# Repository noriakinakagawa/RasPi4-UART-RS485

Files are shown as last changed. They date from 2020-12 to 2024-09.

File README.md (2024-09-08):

# RasPi4-UART-RS485
Raspberry Pi 4 のUART 5chをRS485に変換したコマンド式サーボモータを動かすための基板データ

## Raspberry Pi OSの場合
/boot/config.txt or /boot/firmware/config.txt

## Ubuntuの場合
/boot/firmware/usercfg.txt

以下を追加して保存・再起動  
dtoverlay=pi3-miniuart-bt  
dtoverlay=uart0  
dtoverlay=uart2  
dtoverlay=uart3  
dtoverlay=uart4  
dtoverlay=uart5  
//init_uart_clock=169600000 // for RasPi5
  
/dev/ttyAMA0~AMA4の5ポートでRS485通信が可能となります。

## 注意事項
RTS信号をTXDから遅延タイマICを介して生成しているため、汎用的に使う場合は考慮が必要です。

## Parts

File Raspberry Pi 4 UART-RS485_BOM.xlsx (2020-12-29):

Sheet: 部品表
Reference | Quantity | Footprint | Datasheet | 購入URL | 型番 | 数量 | 購入先 | 製造数 | 5 | カゴチェック | 代替品を使う場合使わない部品
> C1-C10 | 0.1u | Capacitors_SMD:C_0603 | ~ | https://www.digikey.jp/product-detail/ja/kemet/C0603C104M4RACTU/399-1099-1-ND/411374 | C0603C104M4RACTU | 10 | Digi-key | 50
D1 | LED | LEDs:LED_0603 | ~ | https://www.digikey.jp/product-detail/ja/lite-on-inc/LTST-C190KRKT/160-1436-1-ND/386816 | LTST-C190KRKT | 1 | Digi-key | 5
> J1-J6 | B4B-EH | Connectors_JST:JST_EH_B4B-EH-A_1x04_P2.50mm_Vertical | ~ | https://www.digikey.jp/product-detail/ja/jst-sales-america-inc/B4B-EH-A-LF-SN/455-1613-ND/758748 | B4B-EH-A(LF)(SN) | 6 | Digi-key | 30
J7 | B2B-XH | Connectors_JST:JST_XH_B2B-XH-A_1x02_P2.50mm_Vertical | ~ | https://akizukidenshi.com/catalog/g/gC-12247/ | B2B-XH-A(LF)(SN | 1 | 秋月電子通商 | 5
J8 | B2B-PH | Connectors_JST:JST_PH_B2B-PH-K_1x02_P2.00mm_Vertical | ~ | https://akizukidenshi.com/catalog/g/gC-12802/ | B2B-PH-K-S(LF)(SN) | 1 | 秋月電子通商 | 5
M1 | Fan | F251R-05LB:F251R-05LB | ~ | https://www.digikey.jp/product-detail/ja/nidec-copal-electronics/F251R-05LB/563-1109-ND/1165503 | F251R-05LB | 1 | Digi-key | 5
M1 | Fan | 鉄＋なべBタイト |  | https://wilco.jp/products/F/FBP-N.html#page3 | FBP-0306N | 4 | ウィルコ | 20
MK2-MK4 | M2.6 | ジュラコンスペーサ |  | https://www.hirosugi-net.co.jp/shop/g/g3654/ | BS-2611E | 3 | ヒロスギネット | 15
MK2-MK4 | M2.6 | 鉄＋なべ小ねじ |  | https://wilco.jp/products/F/F-N.html#page3 | F-2606N | 3 | ウィルコ | 15
P1 | Conn_02x20 | Connector_PinSocket_2.54mm:PinSocket_2x20_P2.54mm_Vertical |  | https://akizukidenshi.com/catalog/g/gC-00085/ | FH-2x20SG | 1 | 秋月電子通商 | 5
> R1-R5 | 470k | Resistors_SMD:R_0603 | ~ | https://www.digikey.jp/product-detail/ja/panasonic-electronic-components/ERJ-3EKF4703V/P470KHCT-ND/1746784 | ERJ-3EKF4703V | 5 | Digi-key | 25
> R6-R8 | 10k | Resistors_SMD:R_0603 | ~ | https://www.digikey.jp/product-detail/ja/te-connectivity-passive-product/CRG0603F10K-10/A121523CT-ND/5246510 | CRG0603F10K/10 | 3 | Digi-key | 15
> U1-U5 | 74LVC1G04 | TO_SOT_Packages_SMD:SOT-353_SC-70-5 | https://assets.nexperia.com/documents/data-sheet/74LVC1G04.pdf | https://www.digikey.jp/product-detail/ja/nexperia-usa-inc/74LVC1G04GW-125/1727-2871-1-ND/763420 | 74LVC1G04GW,125 | 5 | Digi-key | 25
> U6-U10 | LTC6994xS6-1 | TO_SOT_Packages_SMD:TSOT-23-6 | https://www.analog.com/media/en/technical-documentation/data-sheets/699412fb.pdf | https://www.digikey.jp/product-detail/ja/analog-devices-inc/LTC6994CS6-1-TRMPBF/LTC6994CS6-1-TRMPBFCT-ND/2404476 | LTC6994CS6-1#TRMPBF | 5 | Digi-key | 25
> U11-U15 | ST1480ACDR | SMD_Packages:SOIC-8-N | https://media.digikey.com/pdf/Data%20Sheets/ST%20Microelectronics%20PDFS/ST1480AB_C_Rev_4.pdf | https://www.digikey.jp/product-detail/ja/stmicroelectronics/ST1480ACDR/497-3726-1-ND/686444 | ST1480ACDR | 5 | Digi-key | 25
U16 | MPU-9250 | MPU-9250:MPU-9250 | https://strawberry-linux.com/pub/mpu-9250-manual.pdf | https://strawberry-linux.com/catalog/items?code=12250 | MPU-9250 | 1 | ストロベリーリナックス | 5
U17 | D24V50F5 | D24V50F5:D24V50F5 | https://www.pololu.com/product/2851 | https://store.shopping.yahoo.co.jp/suzakulab/pololu-2851.html | D24V50F5 | 1 | 朱雀技研 | 5

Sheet: 発注表_Digi-key
Reference | Quantity | Footprint | Datasheet | 購入URL | 型番 | 数量 | 購入先 | 製造数 | 5 | カゴチェック | 代替品を使う場合使わない部品
> C1-C10 | 0.1u | Capacitors_SMD:C_0603 | ~ | https://www.digikey.jp/product-detail/ja/kemet/C0603C104M4RACTU/399-1099-1-ND/411374 | C0603C104M4RACTU | 10 | Digi-key | 50
D1 | LED | LEDs:LED_0603 | ~ | https://www.digikey.jp/product-detail/ja/lite-on-inc/LTST-C190KRKT/160-1436-1-ND/386816 | LTST-C190KRKT | 1 | Digi-key | 5
> J1-J6 | B4B-EH | Connectors_JST:JST_EH_B4B-EH-A_1x04_P2.50mm_Vertical | ~ | https://www.digikey.jp/product-detail/ja/jst-sales-america-inc/B4B-EH-A-LF-SN/455-1613-ND/758748 | B4B-EH-A(LF)(SN) | 6 | Digi-key | 30
M1 | Fan | F251R-05LB:F251R-05LB | ~ | https://www.digikey.jp/product-detail/ja/nidec-copal-electronics/F251R-05LB/563-1109-ND/1165503 | F251R-05LB | 1 | Digi-key | 5
> R1-R5 | 470k | Resistors_SMD:R_0603 | ~ | https://www.digikey.jp/product-detail/ja/panasonic-electronic-components/ERJ-3EKF4703V/P470KHCT-ND/1746784 | ERJ-3EKF4703V | 5 | Digi-key | 25
> R6-R8 | 10k | Resistors_SMD:R_0603 | ~ | https://www.digikey.jp/product-detail/ja/te-connectivity-passive-product/CRG0603F10K-10/A121523CT-ND/5246510 | CRG0603F10K/10 | 3 | Digi-key | 15
> U1-U5 | 74LVC1G04 | TO_SOT_Packages_SMD:SOT-353_SC-70-5 | https://assets.nexperia.com/documents/data-sheet/74LVC1G04.pdf | https://www.digikey.jp/product-detail/ja/nexperia-usa-inc/74LVC1G04GW-125/1727-2871-1-ND/763420 | 74LVC1G04GW,125 | 5 | Digi-key | 25
> U6-U10 | LTC6994xS6-1 | TO_SOT_Packages_SMD:TSOT-23-6 | https://www.analog.com/media/en/technical-documentation/data-sheets/699412fb.pdf | https://www.digikey.jp/product-detail/ja/analog-devices-inc/LTC6994CS6-1-TRMPBF/LTC6994CS6-1-TRMPBFCT-ND/2404476 | LTC6994CS6-1#TRMPBF | 5 | Digi-key | 25
> U11-U15 | ST1480ACDR | SMD_Packages:SOIC-8-N | https://media.digikey.com/pdf/Data%20Sheets/ST%20Microelectronics%20PDFS/ST1480AB_C_Rev_4.pdf | https://www.digikey.jp/product-detail/ja/stmicroelectronics/ST1480ACDR/497-3726-1-ND/686444 | ST1480ACDR | 5 | Digi-key | 25

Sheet: 部品表_その他
Reference | Quantity | Footprint | Datasheet | 購入URL | 型番 | 数量 | 購入先 | 製造数 | 5 | カゴチェック | 代替品を使う場合使わない部品
J7 | B2B-XH | Connectors_JST:JST_XH_B2B-XH-A_1x02_P2.50mm_Vertical | ~ | https://akizukidenshi.com/catalog/g/gC-12247/ | B2B-XH-A(LF)(SN | 1 | 秋月電子通商 | 5
J8 | B2B-PH | Connectors_JST:JST_PH_B2B-PH-K_1x02_P2.00mm_Vertical | ~ | https://akizukidenshi.com/catalog/g/gC-12802/ | B2B-PH-K-S(LF)(SN) | 1 | 秋月電子通商 | 5
P1 | Conn_02x20 | Connector_PinSocket_2.54mm:PinSocket_2x20_P2.54mm_Vertical |  | https://akizukidenshi.com/catalog/g/gC-00085/ | FH-2x20SG | 1 | 秋月電子通商 | 5
M1 | Fan | 鉄＋なべBタイト |  | https://wilco.jp/products/F/FBP-N.html#page3 | FBP-0306N | 4 | ウィルコ | 20
MK2-MK4 | M2.6 | 鉄＋なべ小ねじ |  | https://wilco.jp/products/F/F-N.html#page3 | F-2606N | 3 | ウィルコ | 15
MK2-MK4 | M2.6 | ジュラコンスペーサ |  | https://www.hirosugi-net.co.jp/shop/g/g3654/ | BS-2611E | 3 | ヒロスギネット | 15
U16 | MPU-9250 | MPU-9250:MPU-9250 | https://strawberry-linux.com/pub/mpu-9250-manual.pdf | https://strawberry-linux.com/catalog/items?code=12250 | MPU-9250 | 1 | ストロベリーリナックス | 5
U17 | D24V50F5 | D24V50F5:D24V50F5 | https://www.pololu.com/product/2851 | https://store.shopping.yahoo.co.jp/suzakulab/pololu-2851.html | D24V50F5 | 1 | 朱雀技研 | 5

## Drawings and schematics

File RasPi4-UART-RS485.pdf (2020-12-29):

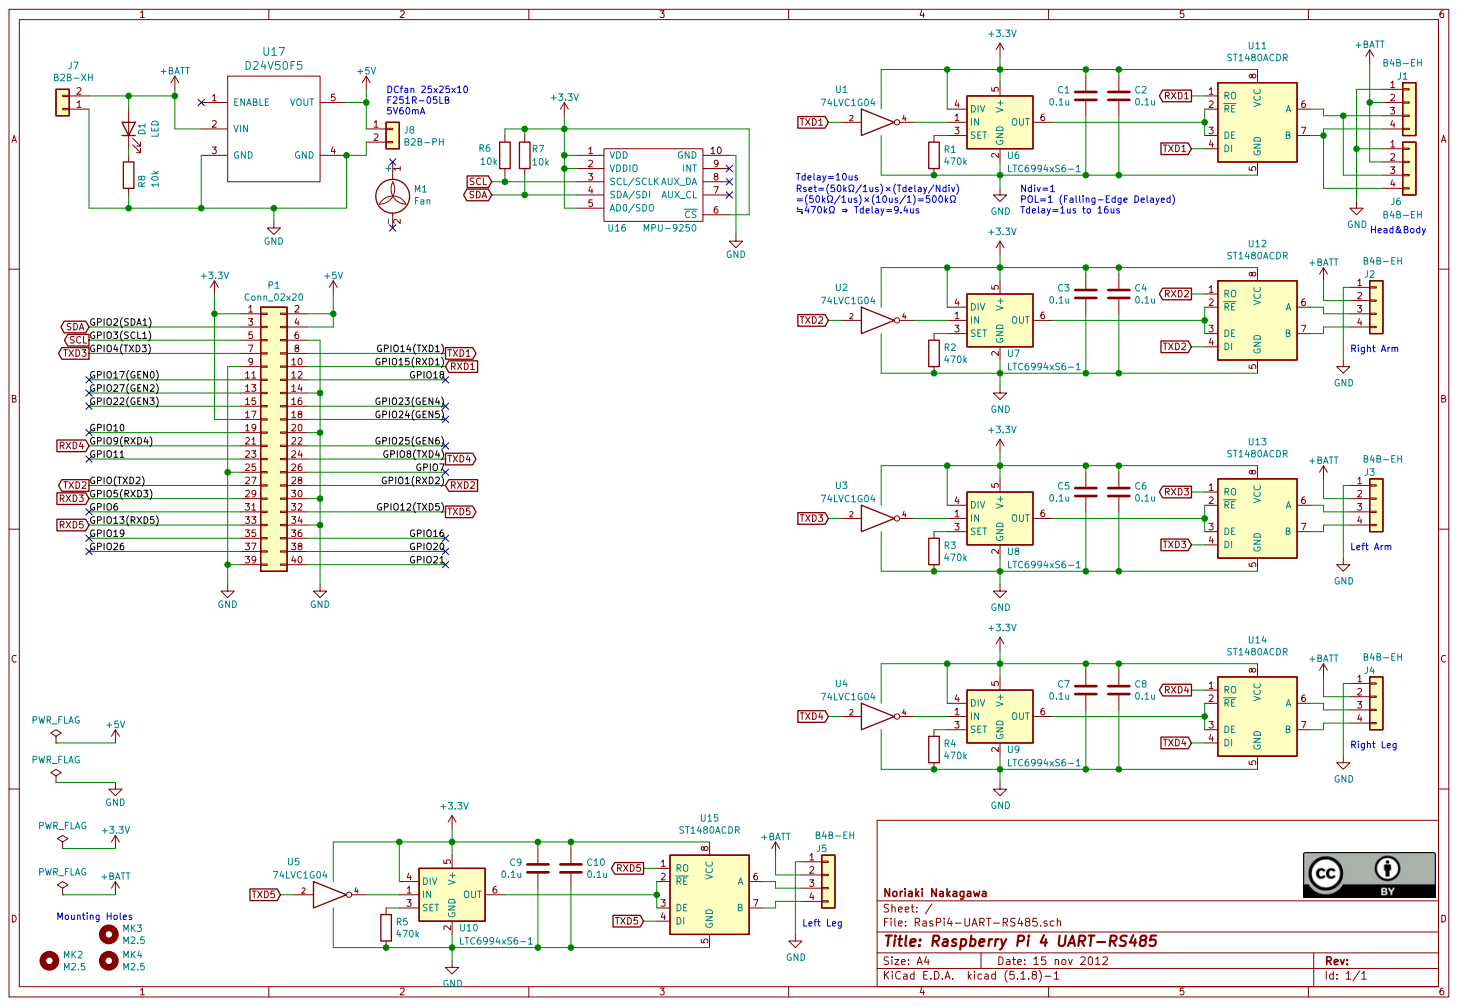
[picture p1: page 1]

LTC6994xS6-1
Ndiv=1 POL=1 (Falling-Edge Delayed)
GND

15 | 16 18 20
17

File: RasPi4-UART-RS485.sch Sheet: / Noriaki Nakagawa

Id: 1/1 Title: Raspberry Pi 4 UART-RS485

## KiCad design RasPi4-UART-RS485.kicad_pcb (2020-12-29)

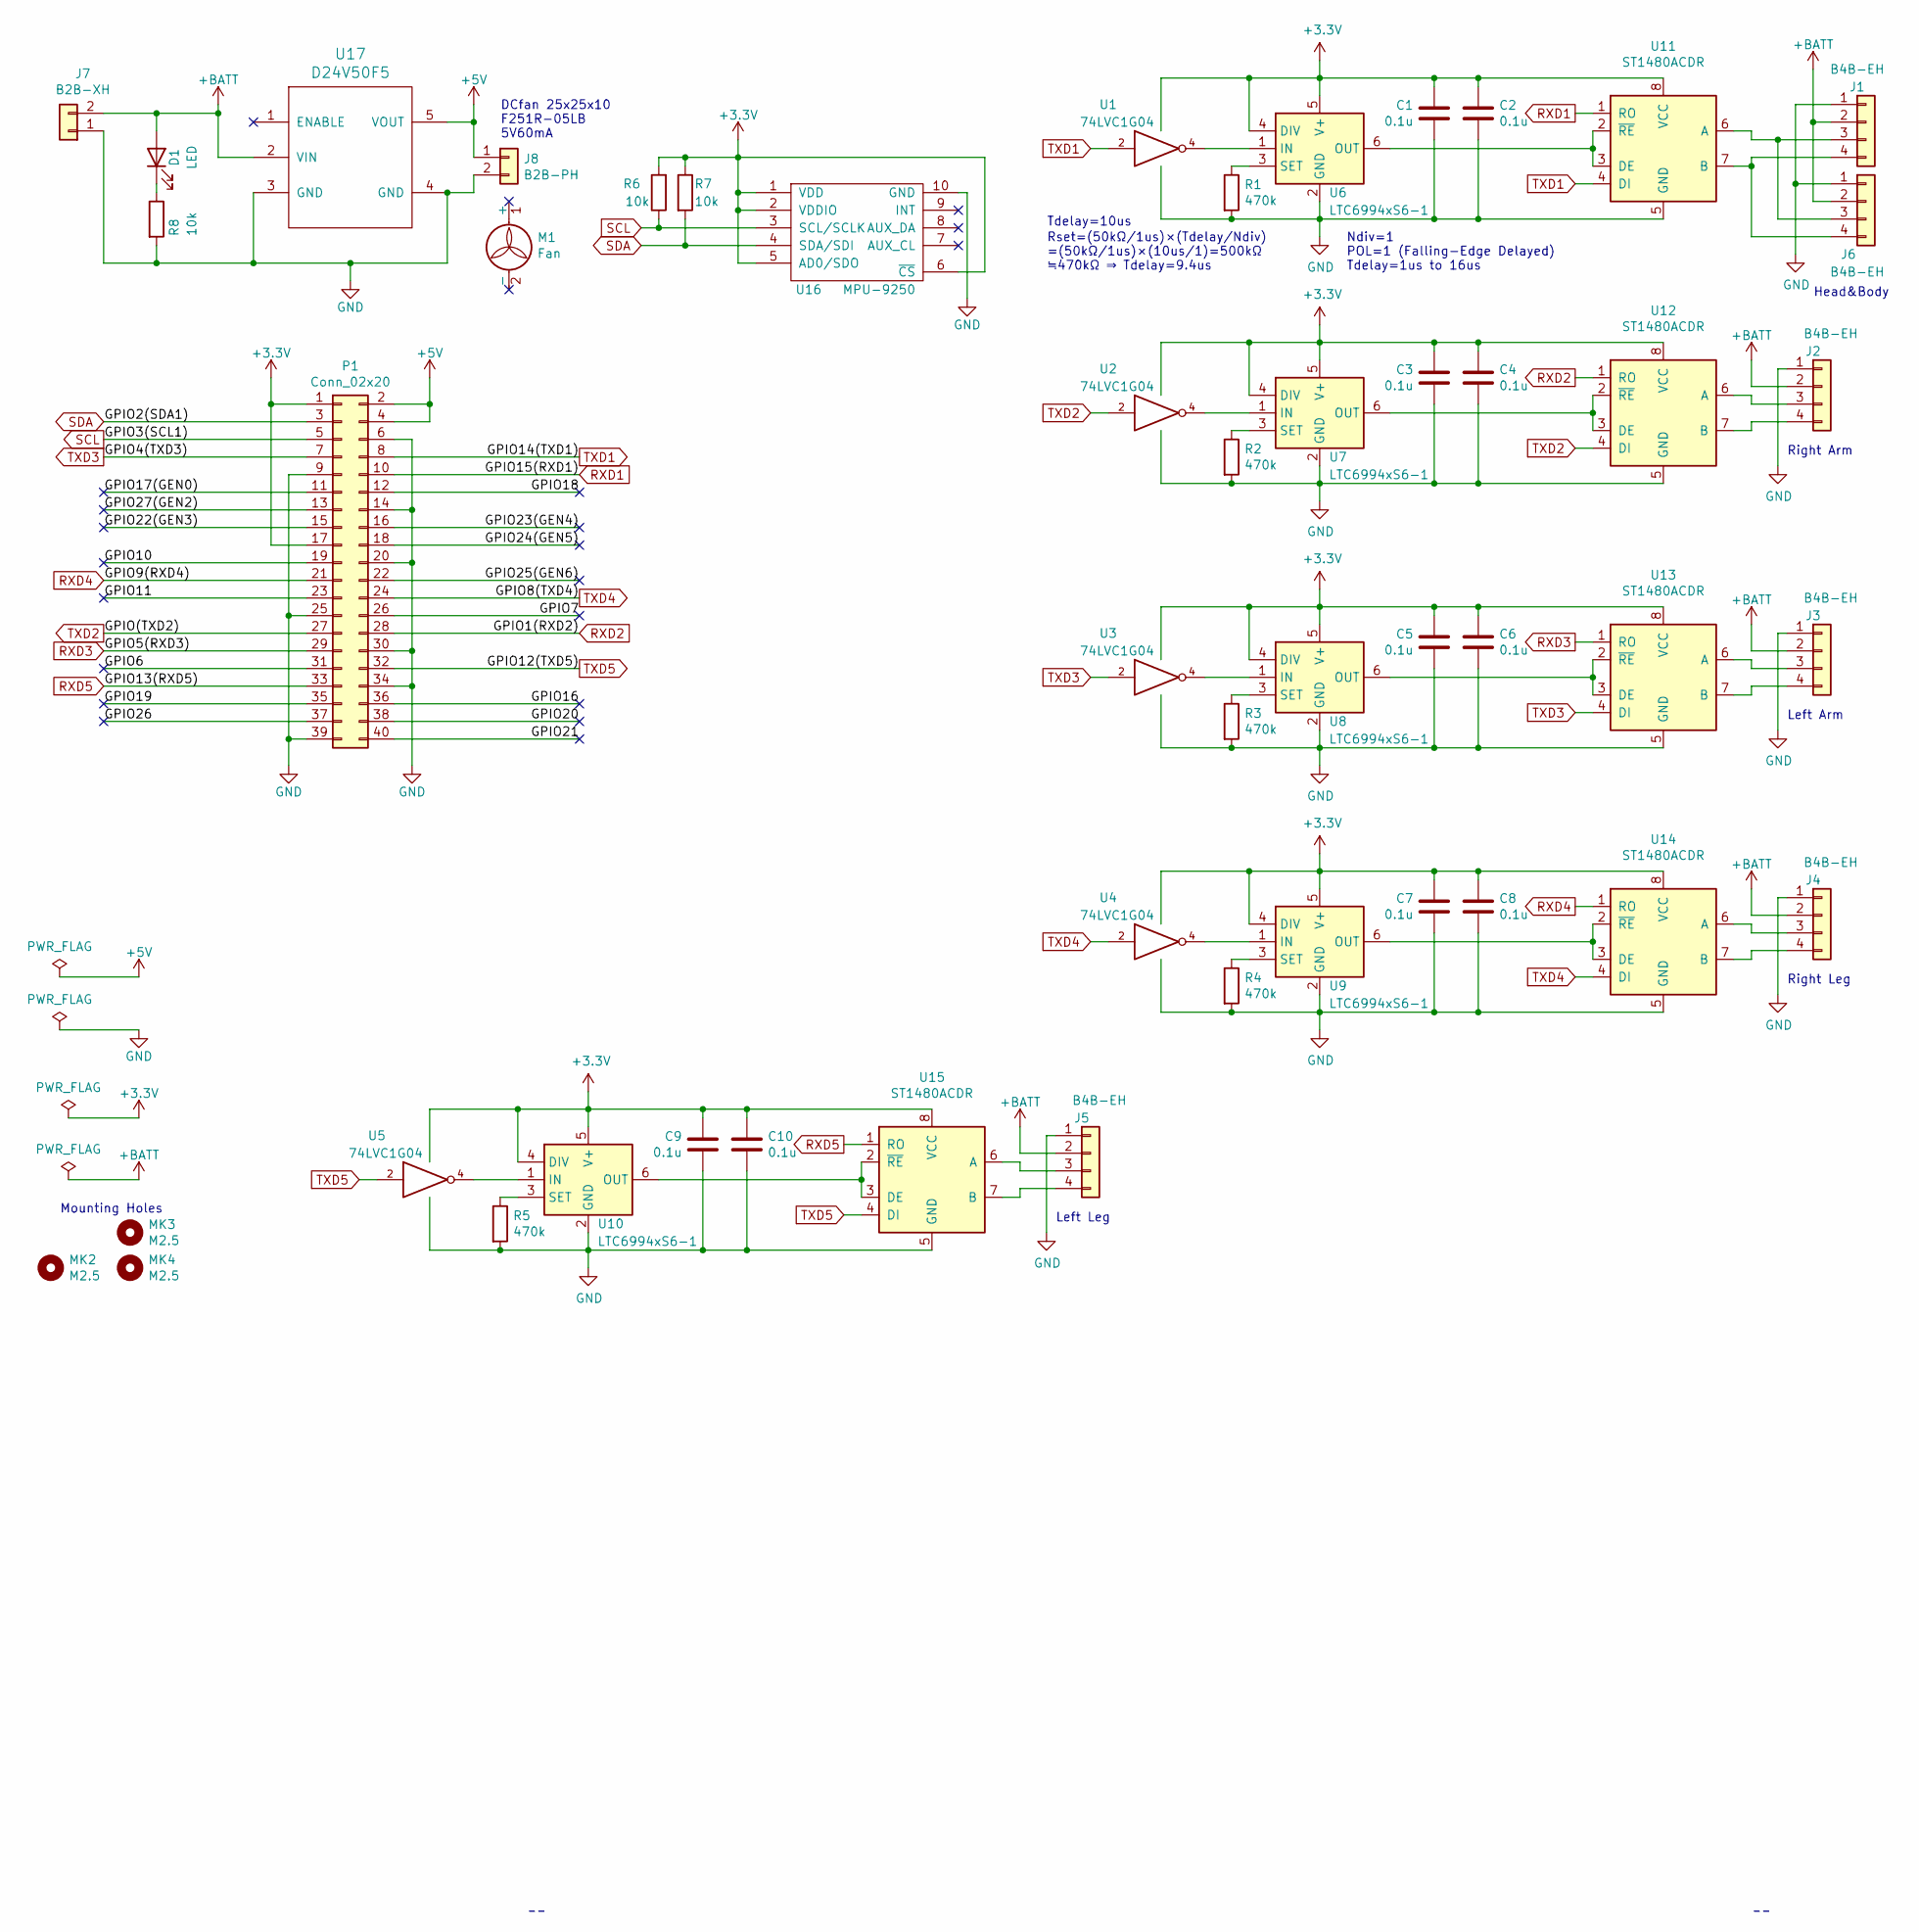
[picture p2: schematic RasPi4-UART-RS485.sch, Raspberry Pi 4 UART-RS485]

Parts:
C1, C2, C3, C4, C5, C6, C7, C8, C9, C10: 0.1u; C_0603
D1: LED; LED_0603
J1, J2, J3, J4, J5, J6: B4B-EH; JST_EH_B4B-EH-A_1x04_P2.50mm_Vertical
J7: B2B-XH; JST_XH_B2B-XH-A_1x02_P2.50mm_Vertical
J8: B2B-PH; JST_PH_B2B-PH-K_1x02_P2.00mm_Vertical
M1: Fan; F251R-05LB
MK2, MK3, MK4: M2.5; MountingHole_2.7mm_M2.5
P1: Conn_02x20; Socket_Strip_Straight_2x20_Pitch2.54mm
R1, R2, R3, R4, R5: 470k; R_0603
R6, R7, R8: 10k; R_0603
U1, U2, U3, U4, U5: 74LVC1G04; SOT-353_SC-70-5
U6, U7, U8, U9, U10: LTC6994xS6-1; TSOT-23-6
U11, U12, U13, U14, U15: ST1480ACDR; SOIC-8_3.9x4.9mm_Pitch1.27mm
U16: MPU-9250
U17: D24V50F5

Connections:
+3V3: C1.1, C2.1, C3.1, C4.1, C5.1, C6.1, C7.1, C8.1, C9.1, C10.1, P1.1, P1.17, R6.2, R7.1, U1.5 (VCC), U2.5 (VCC), U3.5 (VCC), U4.5 (VCC), U5.5 (VCC), U6.4 (DIV), U6.5 (V+), U7.4 (DIV), U7.5 (V+), U8.4 (DIV), U8.5 (V+), U9.4 (DIV), U9.5 (V+), U10.4 (DIV), U10.5 (V+), U11.8 (VCC), U12.8 (VCC), U13.8 (VCC), U14.8 (VCC), U15.8 (VCC), U16.1 (VDD), U16.2 (VDDIO), U16.5 (AD0/SDO), U16.6 (~CS)
+5V: J8.1, P1.2, P1.4, U17.5 (VOUT)
+BATT: D1.2 (A), J1.2, J2.2, J3.2, J4.2, J5.2, J6.2, J7.2, U17.2 (VIN)
/GPIO6: P1.31
/GPIO7: P1.26
/GPIO10: P1.19
/GPIO11: P1.23
/GPIO16: P1.36
/GPIO17(GEN0): P1.11
/GPIO18: P1.12
/GPIO19: P1.35
/GPIO20: P1.38
/GPIO21: P1.40
/GPIO22(GEN3): P1.15
/GPIO23(GEN4): P1.16
/GPIO24(GEN5): P1.18
/GPIO25(GEN6): P1.22
/GPIO26: P1.37
/GPIO27(GEN2): P1.13
GND: C1.2, C2.2, C3.2, C4.2, C5.2, C6.2, C7.2, C8.2, C9.2, C10.2, J1.1, J2.1, J3.1, J4.1, J5.1, J6.1, J7.1, J8.2, P1.6, P1.9, P1.14, P1.20, P1.25, P1.30, P1.34, P1.39, R1.2, R2.2, R3.2, R4.2, R5.2, R8.2, U1.3 (GND), U2.3 (GND), U3.3 (GND), U4.3 (GND), U5.3 (GND), U6.2 (GND), U7.2 (GND), U8.2 (GND), U9.2 (GND), U10.2 (GND), U11.5 (GND), U12.5 (GND), U13.5 (GND), U14.5 (GND), U15.5 (GND), U16.10 (GND), U17.3 (GND), U17.4 (GND)
unnamed: D1.1 (K), R8.1
unnamed: J1.3, J6.3, U11.6 (A)
unnamed: J1.4, J6.4, U11.7 (B)
unnamed: J2.3, U12.6 (A)
unnamed: J2.4, U12.7 (B)
unnamed: J3.3, U13.6 (A)
unnamed: J3.4, U13.7 (B)
unnamed: J4.3, U14.6 (A)
unnamed: J4.4, U14.7 (B)
unnamed: J5.3, U15.6 (A)
unnamed: J5.4, U15.7 (B)
unnamed: R1.1, U6.3 (SET)
unnamed: R2.1, U7.3 (SET)
unnamed: R3.1, U8.3 (SET)
unnamed: R4.1, U9.3 (SET)
unnamed: R5.1, U10.3 (SET)
unnamed: U1.4, U6.1 (IN)
unnamed: U2.4, U7.1 (IN)
unnamed: U3.4, U8.1 (IN)
unnamed: U4.4, U9.1 (IN)
unnamed: U5.4, U10.1 (IN)
unnamed: U10.6 (OUT), U15.2 (~RE~), U15.3 (DE)
unnamed: U6.6 (OUT), U11.2 (~RE~), U11.3 (DE)
unnamed: U7.6 (OUT), U12.2 (~RE~), U12.3 (DE)
unnamed: U8.6 (OUT), U13.2 (~RE~), U13.3 (DE)
unnamed: U9.6 (OUT), U14.2 (~RE~), U14.3 (DE)
RXD1: P1.10, U11.1 (RO)
RXD2: P1.28, U12.1 (RO)
RXD3: P1.29, U13.1 (RO)
RXD4: P1.21, U14.1 (RO)
RXD5: P1.33, U15.1 (RO)
SCL: P1.5, R6.1, U16.3 (SCL/SCLK)
SDA: P1.3, R7.2, U16.4 (SDA/SDI)
TXD1: P1.8, U1.2, U11.4 (DI)
TXD2: P1.27, U2.2, U12.4 (DI)
TXD3: P1.7, U3.2, U13.4 (DI)
TXD4: P1.24, U4.2, U14.4 (DI)
TXD5: P1.32, U5.2, U15.4 (DI)

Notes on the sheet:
Mounting Holes
Tdelay=10us
Rset=(50kΩ/1us)×(Tdelay/Ndiv) =(50kΩ/1us)×(10us/1)=500kΩ ≒470kΩ ⇒ Tdelay=9.4us
Ndiv=1 POL=1 (Falling-Edge Delayed) Tdelay=1us to 16us
Head&Body
Right Arm
Left Arm
Right Leg
Left Leg
DCfan 25x25x10 F251R-05LB 5V60mA

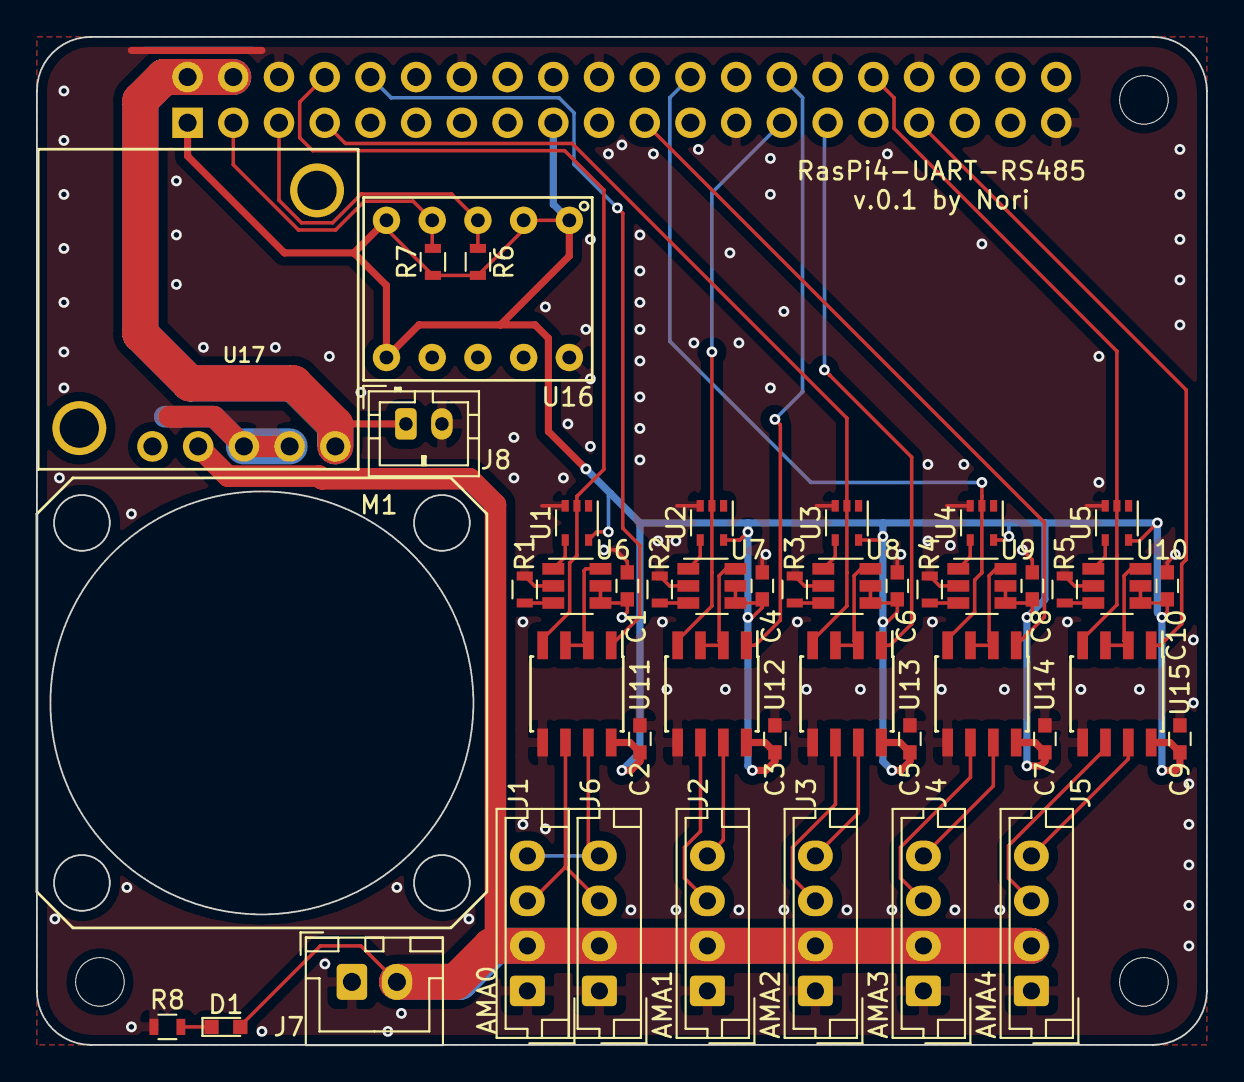
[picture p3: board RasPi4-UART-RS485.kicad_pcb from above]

Board: 2 copper layers, 65.0 x 56.0 mm, 49 parts (1 on the bottom side), 42 nets.

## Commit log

2020-12-29 最初のアップロード
    [RasPi4-UART-RS485.kicad_pcb, RasPi4-UART-RS485.sch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]
2020-12-29 BOM uploard
    [Raspberry Pi 4 UART-RS485_BOM.xlsx]
